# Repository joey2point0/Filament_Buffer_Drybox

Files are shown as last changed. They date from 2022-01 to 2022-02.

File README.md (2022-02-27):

# Filament Buffer Drybox - BETA

This buffer solution is still heavliy in beta, changes to the design will come out as issues and areas of improvement are identified.

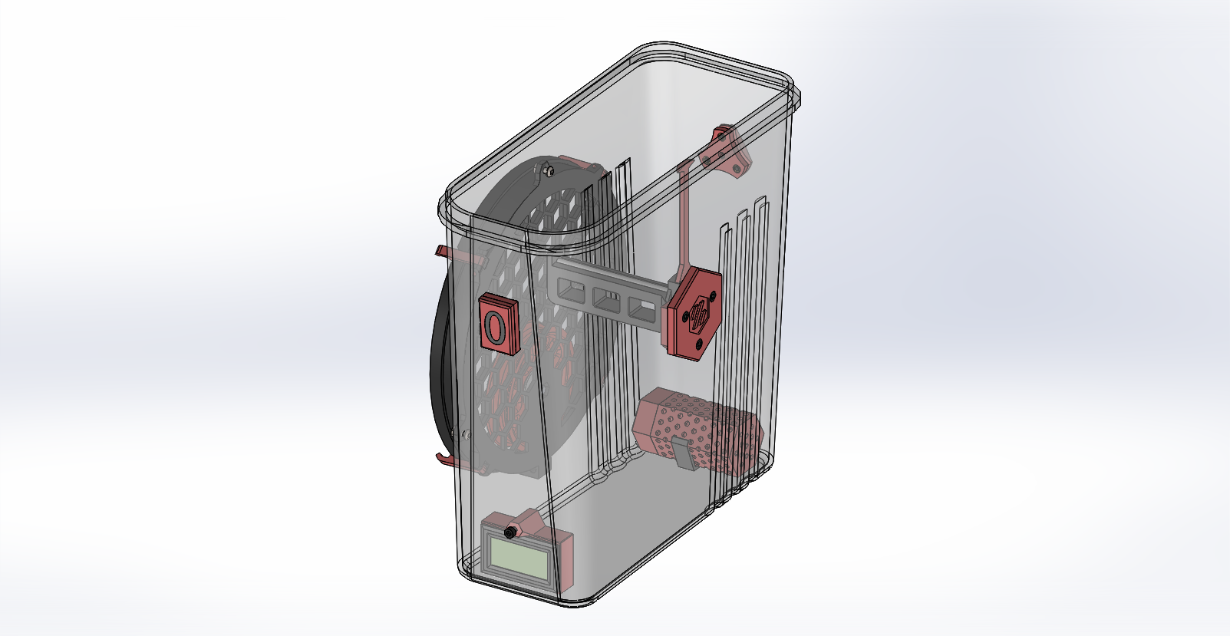
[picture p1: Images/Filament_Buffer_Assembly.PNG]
Filament Buffer Assembly


## BOM

- 4L Air Tight Container
    - The one used for the initial design is [4L Container](https://www.amazon.com/Containers-PRAKI-Airtight-Leak-proof-Canister/dp/B08TWH2QHV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). HOWEVER it was found that the KVP spools had clearance issues. With the help of discord members I am currently looking into alternative options.
	- Containers [6.3L Container](https://www.amazon.com/dp/B08VHMS3B5?psc=1&ref=ppx_yo2_dt_b_product_details) will fit KVP spools but are significantly larger
- 6x (or 3x) M3x.05 heat set inserts
- 8x M3x8 BHCS
- 3x M3 hex nuts
- 3x M3x8 BHCS
- 1x M5x16 BHCS
- 1x M5 nylon lock nut
- Optional
    - Hydrometer
    - Silica
    - 2x 6x3 magenets
    - VHB tape

# Assembly

Spool hanger, filament passthru and buffer are mandatory, desiccant and hydrometer are optional

---
### Important
### The mounting locations described below are what I used, due to wide variety of container and spool sizes, your milage may vary. Confirm fitment before drilling holes.
---
## Filament Passthru

Two variations; one using heat set inserts and the other forms threads in the plastic.

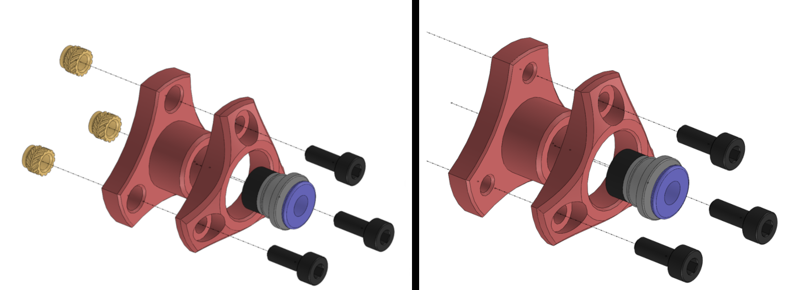
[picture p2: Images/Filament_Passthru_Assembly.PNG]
Filament Passthru Assembly


Assembly

1.  Measure approximately 182mm from the bottom of the container and mark the middle.
2.  Drill a 1/2" hole
3.  Insert the Filliment\_Passthru\_Interior.STL.
4.  Mark the three fastener holes
5.  Remove the Filliment\_Passthru\_Interior.STL and drill (hole size)
6.  Assemble

## Spool Hanger

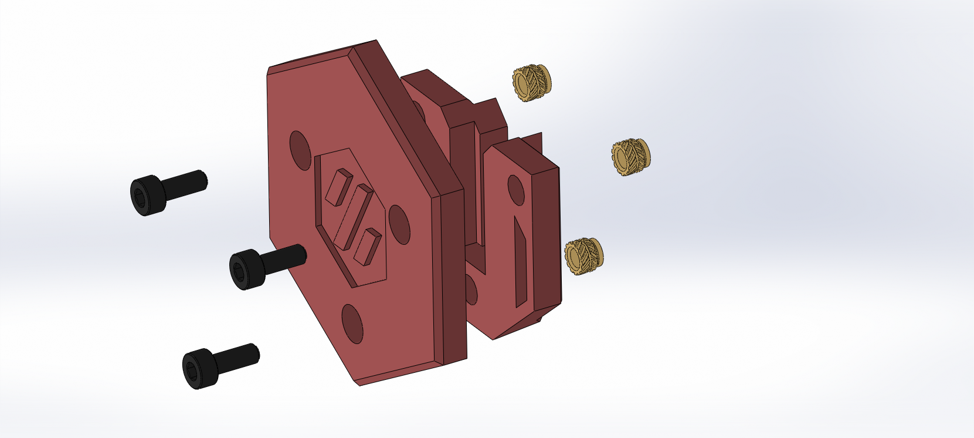
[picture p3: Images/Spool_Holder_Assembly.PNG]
Spool Holder Assembly

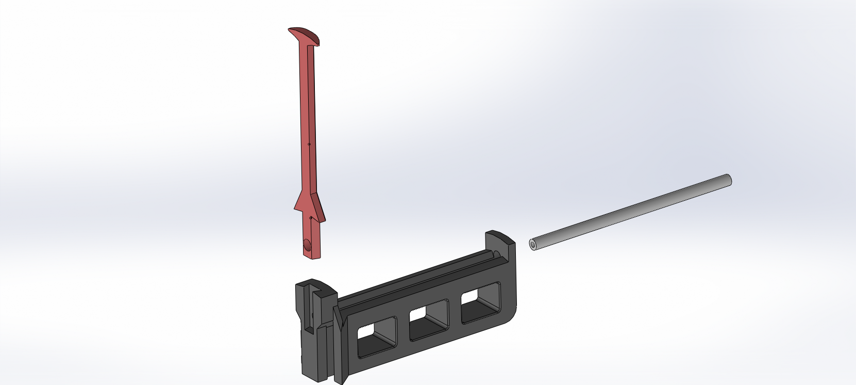
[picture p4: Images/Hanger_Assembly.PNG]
Hanger Assembly


Assembly

1.  Slide the Hanger\_Handle.STL into the slot on the Spool\_Arm.STL and install the PTFE tube to lock it into place

Mounting

1.  Measure approximately 119mm from the bottom of the container and mark the middle.
2.  Drill a 1/8" hole and hang the \[a\]\_Spool\_Arm_Exterior.STL using the bottom screw hole.
3.  Orient the \[a\]\_Spool\_Arm_Exterior.STL so that the edges are relatively square to the bottom of the container
4.  Mark the two remaining holes and drill.
5.  Mount the Assembly, sandwiching the container in between \[a\]\_Spool\_Arm\_Exterior.STL and \[a\]\_Spool\_Arm\_Catch.STL

### Future Design Considerations

Catch clearance and longevity of current design

## Filament Buffer

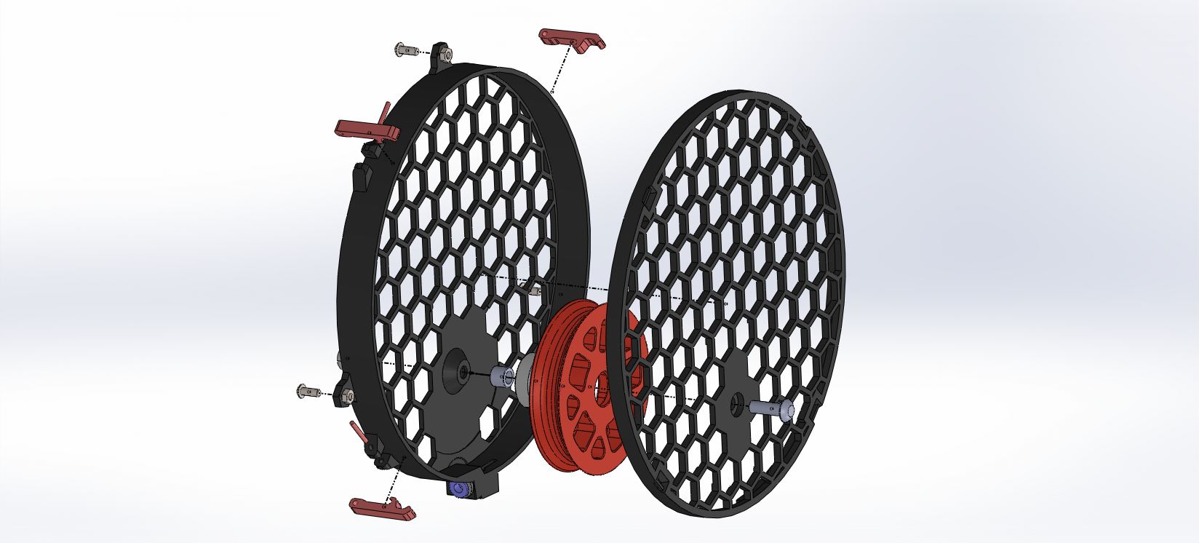
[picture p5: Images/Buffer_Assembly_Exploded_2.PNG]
Buffer Assembly Exploded 2

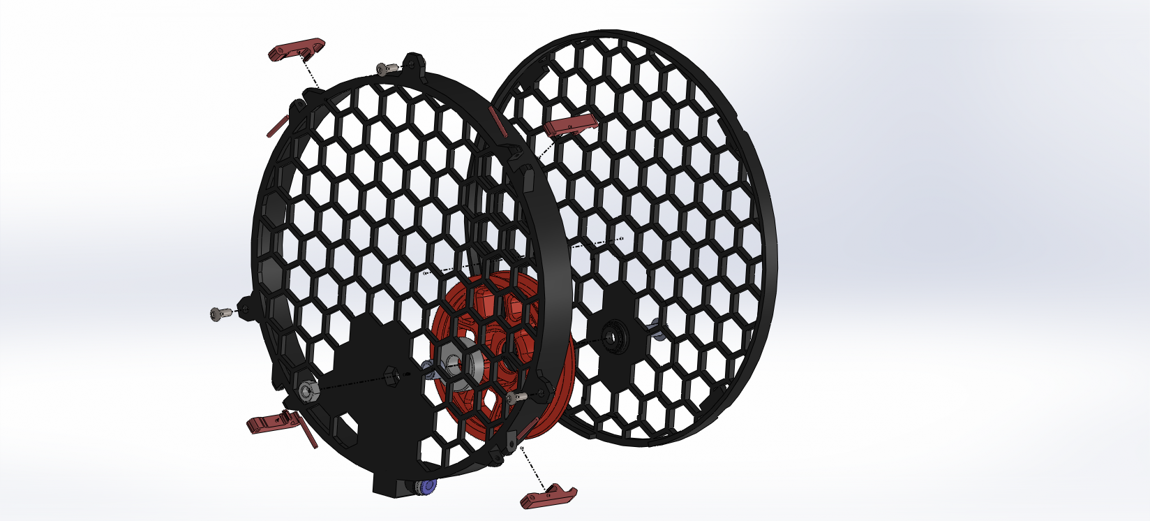
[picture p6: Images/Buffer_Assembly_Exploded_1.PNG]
Buffer Assembly Exploded 1


Assembly

1.  Install the \[a\]\_Buffer\_Latch\_x4.STLs around the perimeter of the Buffer\_Case.STL using a piece of filament as the hinge
2.  press the bearing insert into the bearing and then the bearing in the Buffer_Wheel.STL
3.  Install the bowden collet into the buffer case.stl

mounting

1.  Measure approximately 222mm from the bottom of the container and mark the middle.
2.  Drill a 1/8" hole and hang the Buffer_Case.STL by the top screw and mark the two remaining holes, then drill
3.  Before mounting with the final two screws install the Nylon lock nut in the recess in the buffer cover.

### Future Design Considerations

Clearances of current design, possibility for future redesign to improve usability 

## Hydrometer (Optional)

A Simple hydrometer bracket that mounts using a single M3x8 SHCS, installed against the bottom interior surface to prevent it from rotating.

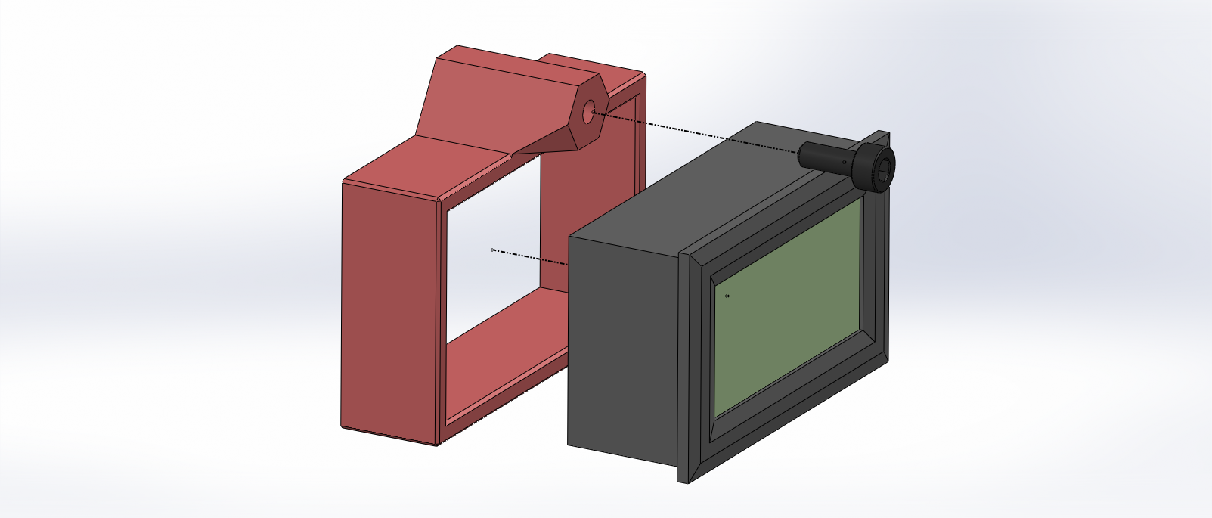
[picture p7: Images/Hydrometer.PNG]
Hydrometer


## Desiccant Pack (Optional)

Mounts in a similar fashion to the hydrometer bracket

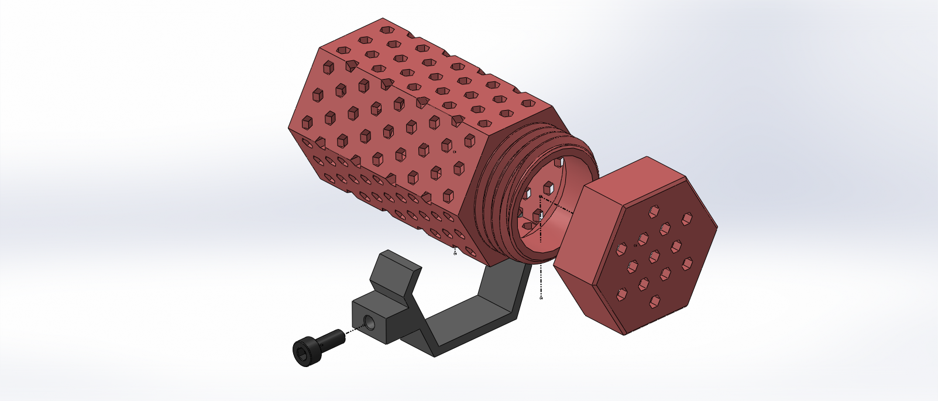
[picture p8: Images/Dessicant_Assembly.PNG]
Dessicant Assembly


# Tag Plate (Optional)

Press in two 6x3 magnets, mounts to container using VHB tape.

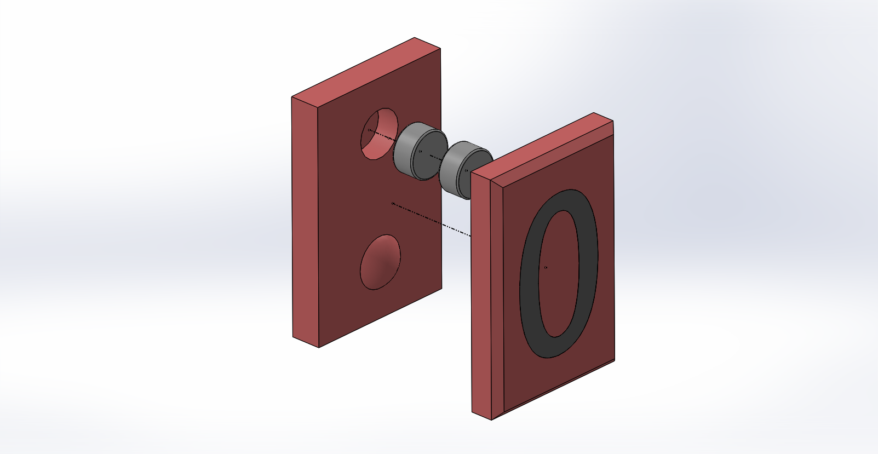
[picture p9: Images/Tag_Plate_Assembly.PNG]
Tag Plate Assembly


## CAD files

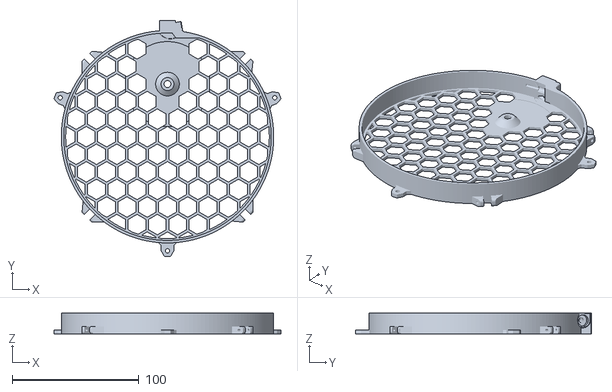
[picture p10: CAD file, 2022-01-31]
STLs/Buffer/Buffer_Case.STL
179.0 x 185.8 x 16.4

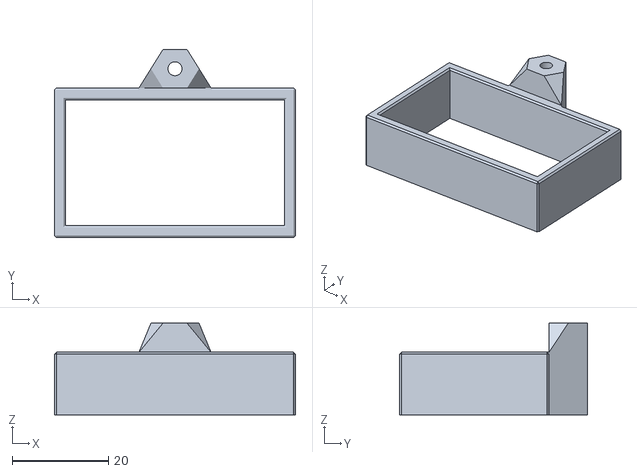
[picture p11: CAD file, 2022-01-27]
STLs/Optional/[a]_Hygrometer_Bracket.STL
50.0 x 39.0 x 19.0

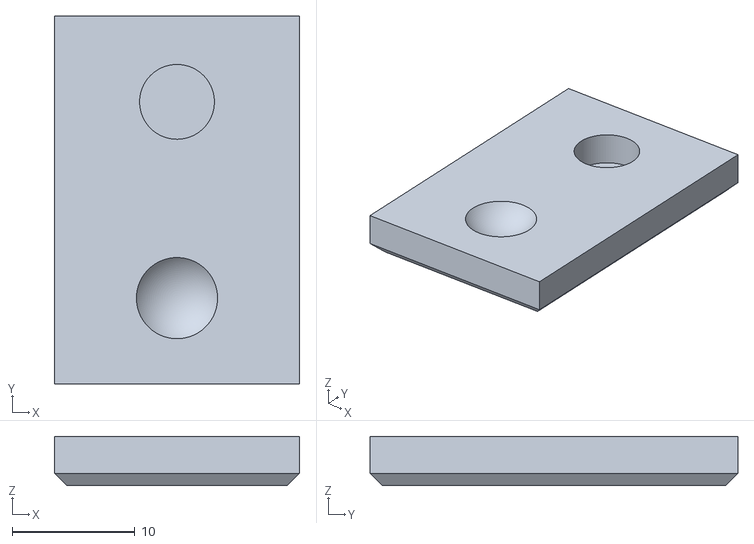
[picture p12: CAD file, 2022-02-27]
STLs/Optional/Tag Plate/[a]_Tag_Plate_6.STL
20.0 x 30.0 x 4.00

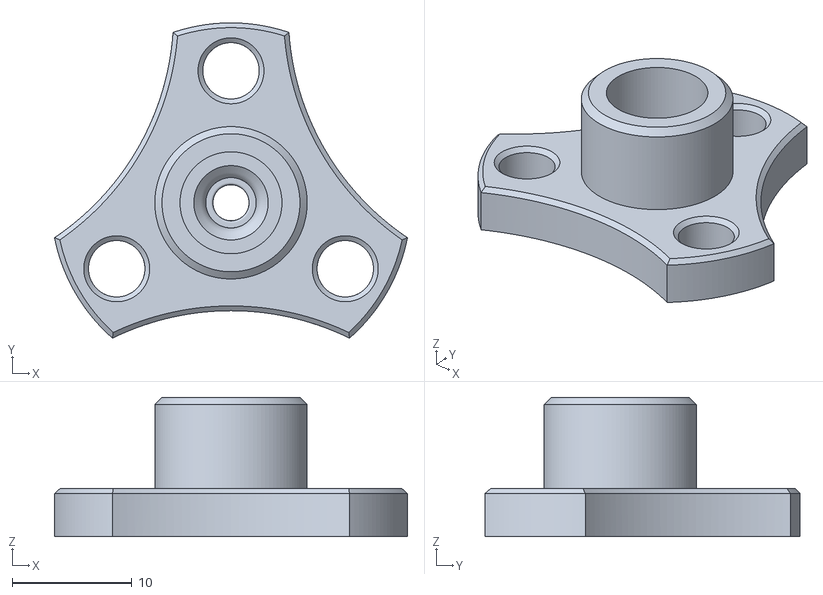
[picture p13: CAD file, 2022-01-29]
STLs/Passthru/[a]_Filament_Passthru_Interior_HeatSet.STL
29.4 x 26.3 x 11.6

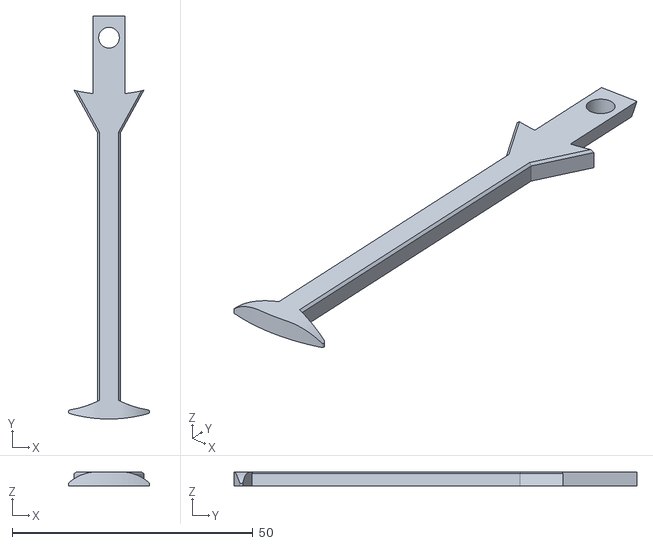
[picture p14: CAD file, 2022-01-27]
STLs/Spool Arm/[a]_Spool_Arm_Handle.STL
16.9 x 83.7 x 3.00

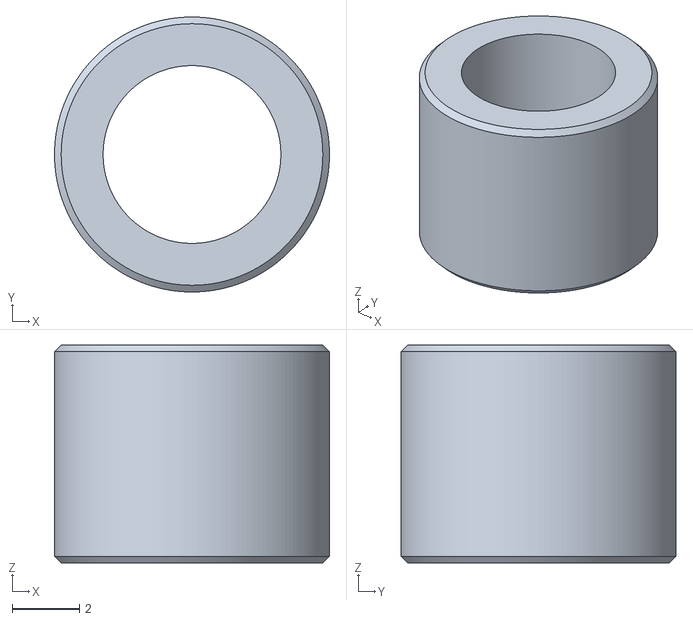
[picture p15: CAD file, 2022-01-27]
STLs/Buffer/Bearing_Adapter.STL
8.20 x 8.20 x 6.50

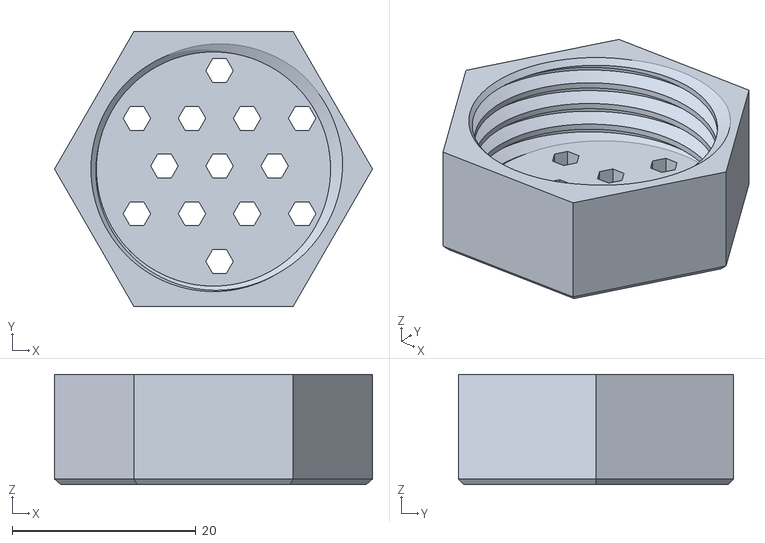
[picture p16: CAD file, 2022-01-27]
STLs/Optional/[a]_Dessicant_Tube_Cap.STL
34.6 x 30.0 x 12.0

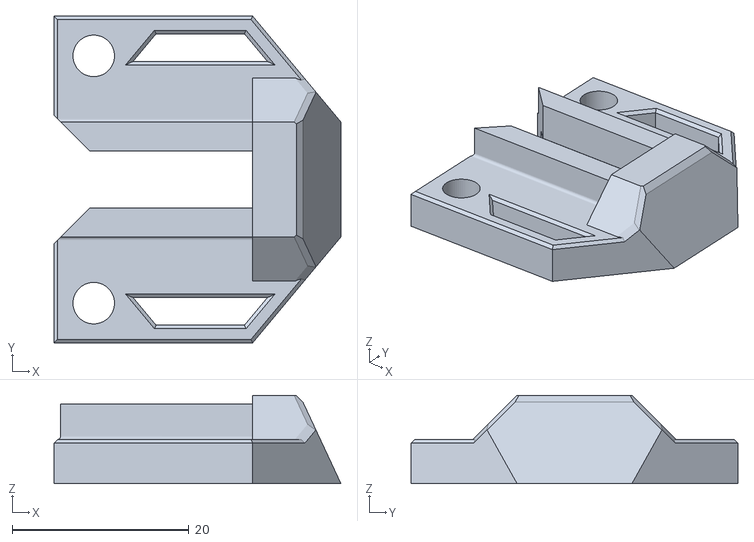
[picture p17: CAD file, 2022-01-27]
STLs/Spool Arm/[a]_Spool_Arm_Catch.STL
32.5 x 37.0 x 10.0

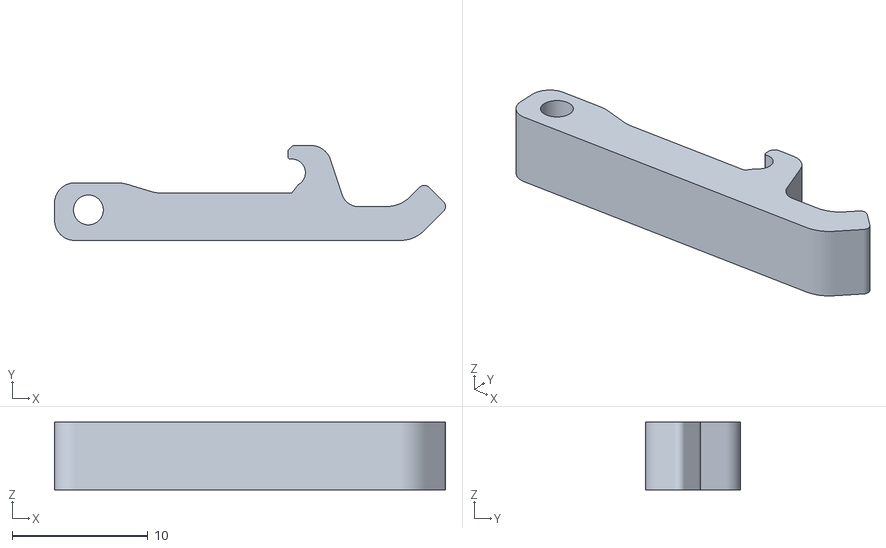
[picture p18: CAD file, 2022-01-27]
STLs/Buffer/[a]_Buffer_Latch_x4.STL
28.8 x 7.00 x 5.00

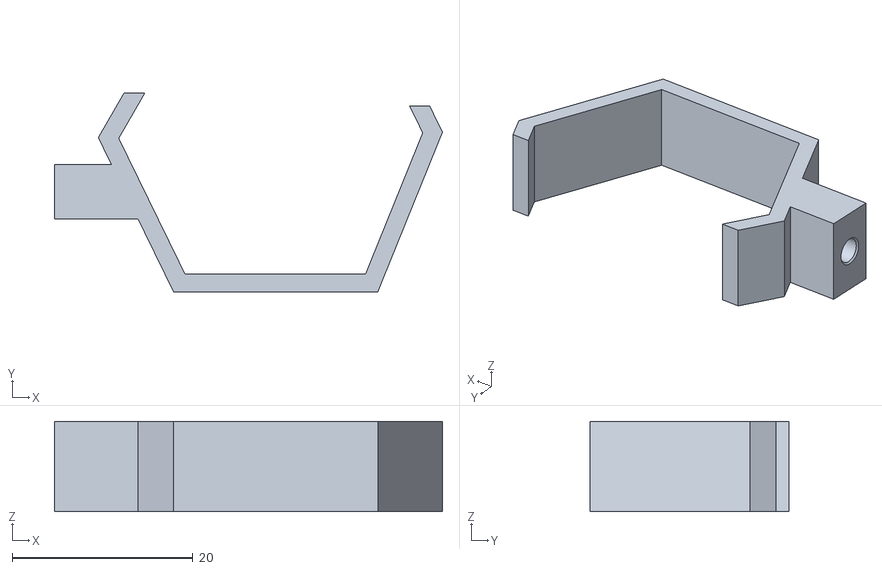
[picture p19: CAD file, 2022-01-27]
STLs/Optional/Dessicant_Tube_Clip.STL
42.9 x 22.0 x 10.0

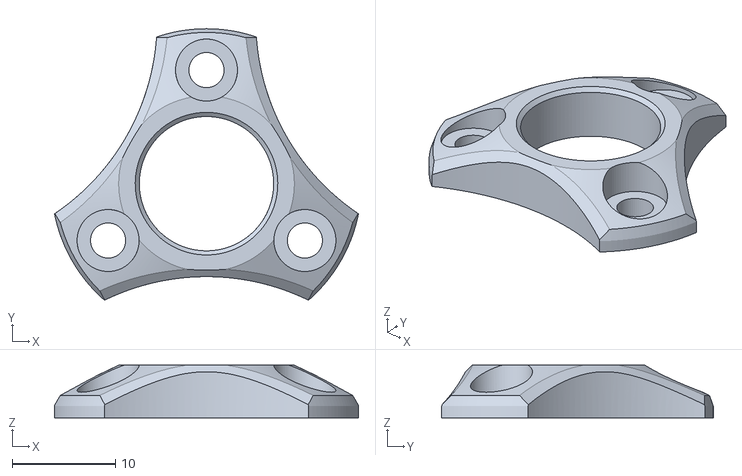
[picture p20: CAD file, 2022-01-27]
STLs/Passthru/[a]_Filament_Passthru_Exterior.STL
29.4 x 26.3 x 5.10

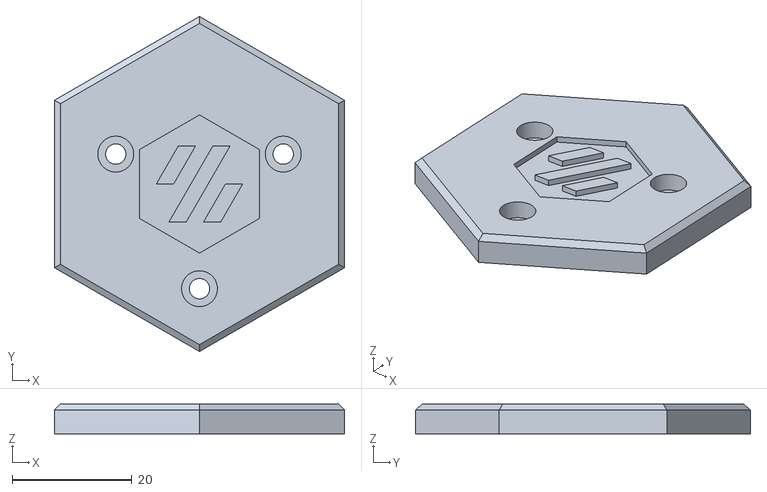
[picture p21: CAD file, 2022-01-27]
STLs/Spool Arm/[a]_Spool_Arm_Exterior.STL
48.5 x 56.0 x 5.00

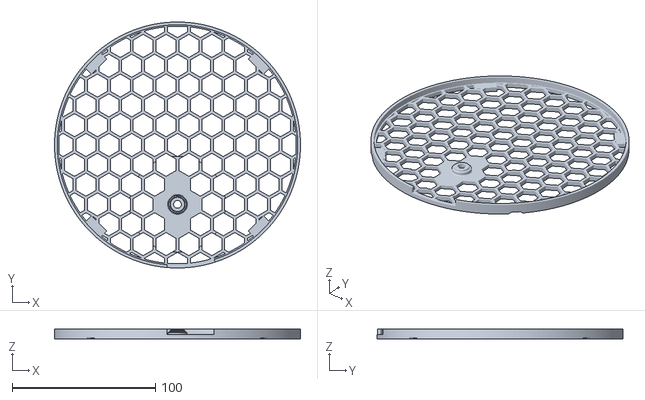
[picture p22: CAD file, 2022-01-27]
STLs/Buffer/Buffer_Cover.STL
172.0 x 172.0 x 7.00

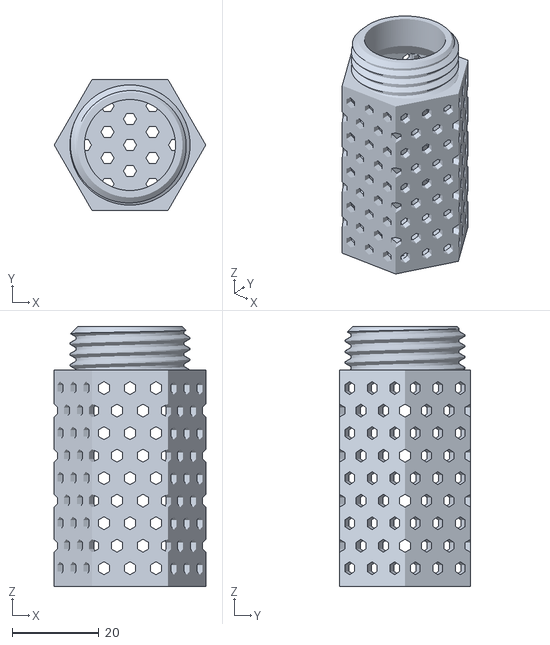
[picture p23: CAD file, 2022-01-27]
STLs/Optional/[a]_Dessicant_Tube_Body.STL
35.0 x 30.3 x 60.0

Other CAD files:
STLs/Optional/Tag Plate/[a]_Tag_Plate_0.STL
STLs/Passthru/[a]_Filament_Passthru_Interior_FormThread.STL
STLs/Optional/Tag Plate/[a]_Tag_Plate_8.STL
STLs/Optional/Tag Plate/[a]_Tag_Plate_1.STL
STLs/Optional/Tag Plate/[a]_Tag_Plate_2.STL
STLs/Optional/Tag Plate/[a]_Tag_Plate_3.STL
STLs/Optional/Tag Plate/[a]_Tag_Plate_4.STL
STLs/Optional/Tag Plate/[a]_Tag_Plate_5.STL
STLs/Optional/Tag Plate/[a]_Tag_Plate_7.STL
STLs/Optional/Tag Plate/[a]_Tag_Plate_Base.STL
STLs/Spool Arm/Spool_Arm.STL

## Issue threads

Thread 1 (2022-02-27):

Suggestion

AnthonySinor, 2022-02-27:
Add an M5 Washer to the BOM.
Make the bolt hole on the Cover 7mm.
This will keep the wheel stationary and allow the cover to be removed for easy loading/unloading.

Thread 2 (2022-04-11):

Changing filament rolls...

maziggy, 2022-04-11:
... is quite uncomfortable. Have to think about this a little bit....
Despite of this I'll love it and currently printing it.

Thanks!

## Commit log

2022-01-27 Add STLs
    [Bearing_Adapter.STL, Buffer_Case.STL, Buffer_Cover.STL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]
2022-01-29 Added passthru variation
    [[a]_Filament_Passthru_Interior_FormThread.STL, [a]_Filament_Passthru_Interior_HeatSet.STL]
2022-01-31 Uneven hex pattern on Buffer_Case.STL
    [Buffer_Case.STL]
2022-02-27 Added Tag Plates
    [[a]_Tag_Plate_0.STL, [a]_Tag_Plate_1.STL, [a]_Tag_Plate_2.STL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]
2022-02-27 Updated main assembly photo
